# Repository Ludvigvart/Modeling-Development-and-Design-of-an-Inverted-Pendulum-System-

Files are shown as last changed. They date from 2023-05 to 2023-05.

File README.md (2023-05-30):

# Modeling-Development-and-Design-of-an-Inverted-Pendulum-System-
Repository for a bachelor's project by a group of students from the Norwegian University of Science and Technology

## About The Project
The inverted pendulum has made its mark as a staple in the field of control theory, making an appearance in classic mechanical systems such as the Furuta pendulum and the cart-pendulum system. This thesis focuses on the reaction wheel pendulum, more specifically the modeling, development and design of an inverted spherical pendulum actuated by two perpendicular reaction wheels. The system is developed with the overarching objective of functioning as an interactive learning platform for testing and experimenting with various control configurations.

The modeling of the system is centered around the derivation of an expression for the dynamics, which is done through the utilization of the Euler-Lagrange equations. The design process integrates a hardware and mechanical design approach, aiming to achieve optimum functionality while minimizing expenditure. Fabrication of the mechanical components entails 3D printing, and the hardware components are intricately connected onto a bespoke PCB. The implementation of the operational functionalities, e.g., Euler angle estimation and control system algorithms, is executed through the usage of the ESP32 family-based microcontroller. Additionally, wireless communication between the microcontroller and a Python-based user interface is established, making the product intuitive and user-friendly. 

<div style="display: flex; justify-content: center;">
  dual_axis_system
</div>

## Programs Used
Fusion 360 by Autodesk was used to design all 3D-printed components for the system. The microcontroller program was written in Arduino C. Altium Designer was used to design the custom PCB.
Python 3.11 was used to create the PC-program. 
* [](https://www.autodesk.no/products/fusion-360/overview)
* [](https://www.arduino.cc/en/software)
* [](https://www.altium.com/altium-designer)
* [](https://www.python.org/)

## Notes Regarding Usage
When uploading new code to microcontroller with a USB cable, it is important that the power switch on the system is in the OFF position. With the power switch ON and a USB cable connected, it is likely that the microcontroller will be damaged, as 5 V then will be supplied from two different sources. 
When charging the batteries, it is recommended that a voltage between 12.6 - 13 V is supplied with a current of approximately 2 A. We suggest that the batteries should always have a charge between 11.1 – 12.6 V to retain suitable motor performance. 

## Notes Regarding Included Files
The finalized microcontroller code can be accessed in the designated Arduino code folder. The CAD models and adjoining G-code files of the system's 3D-printed parts are made accessible within the CAD folder. The design files for the custom PCB are available under the PCB folder. A compiled executable "Inverted Pendulum Interface.exe" of the PC-program is also provided, along the full Python code. Regarding the PC-program it is worth mentioning that it’s intended to work on any Windows 10/11 PC with a screen resolution of 1920x1080 and a scaling factor set to 100%.

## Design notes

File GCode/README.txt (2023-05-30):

The G-Code files are ready to use with the settings used under the project. The last number in the file name pertains to percent infill. The 3D-print machines used are the Ultimaker 2 Extended+ series. They can also be printed on a normal Ultimaker 2+, except for the pendulums.

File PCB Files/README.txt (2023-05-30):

This folder contains the Altium Designer project files "BSc_PCB_balanserande_pinne", and a complete zip file "Gerber.rar" of all necessary Gerber files needed for production by a PCB manufacturer.

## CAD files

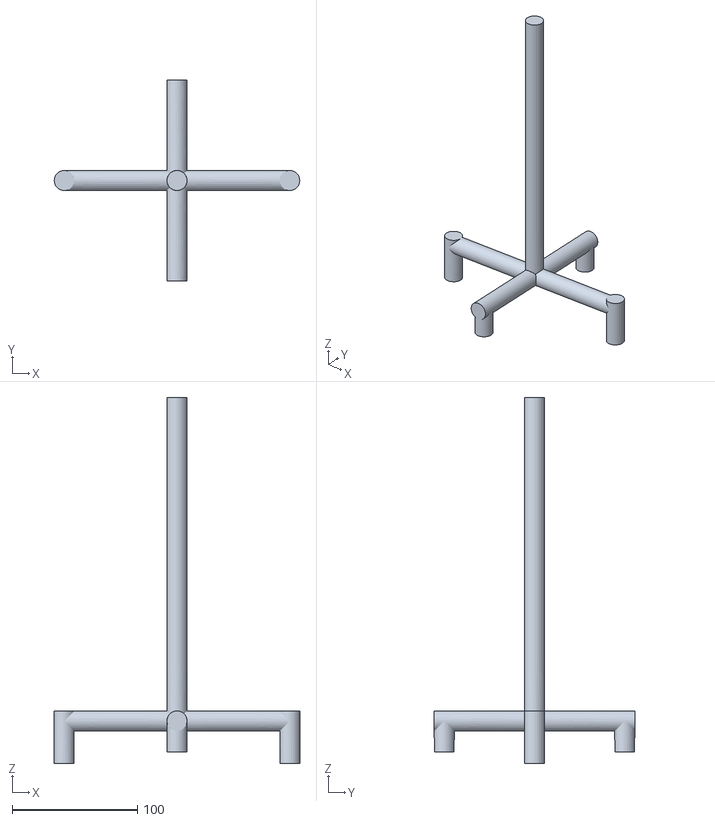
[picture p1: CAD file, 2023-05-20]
STL Files/Quad-Ended Pendulum v1.stl
196.0 x 160.0 x 292.0

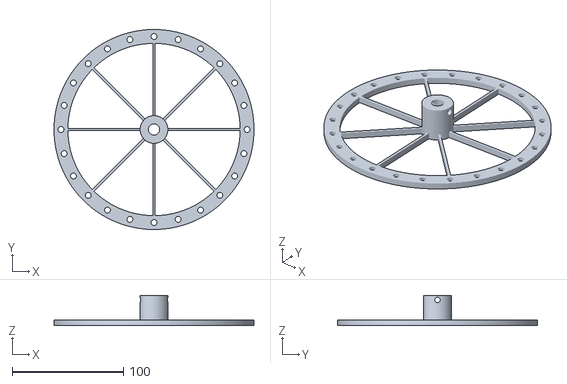
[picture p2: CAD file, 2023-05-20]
STL Files/Reaction Wheel v1.stl
180.0 x 180.0 x 27.0

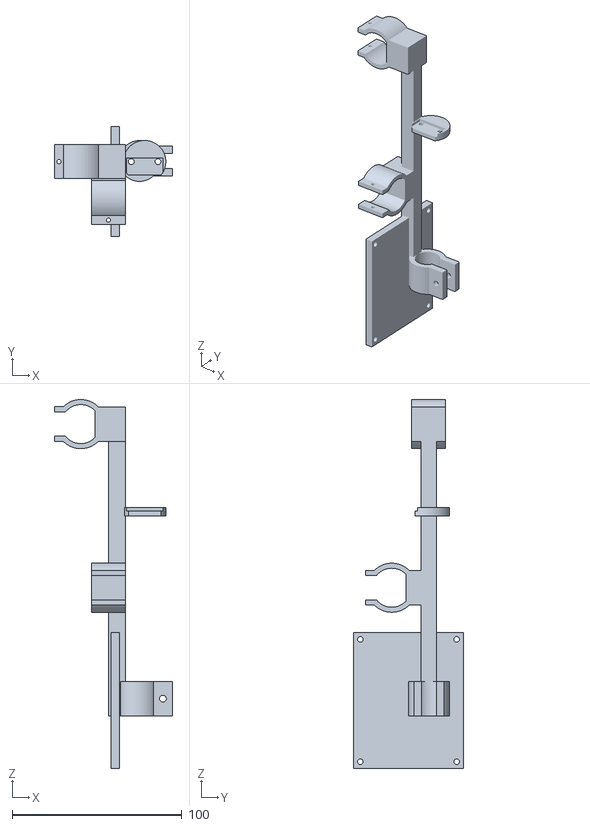
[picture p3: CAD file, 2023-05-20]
STL Files/Frame v3.stl
69.6 x 64.8 x 217.6

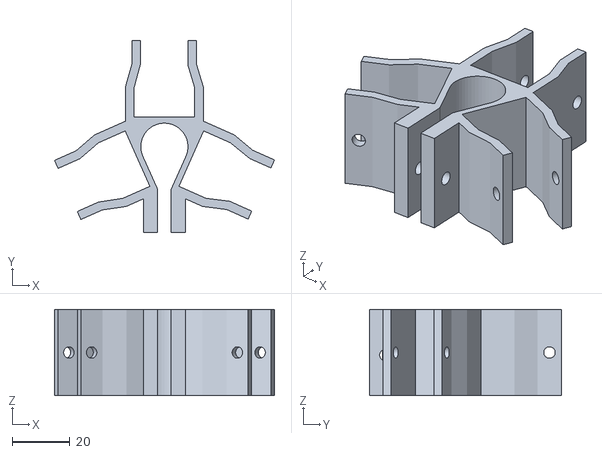
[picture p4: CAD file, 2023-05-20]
STL Files/Battery Mount v1.stl
76.5 x 66.7 x 30.0

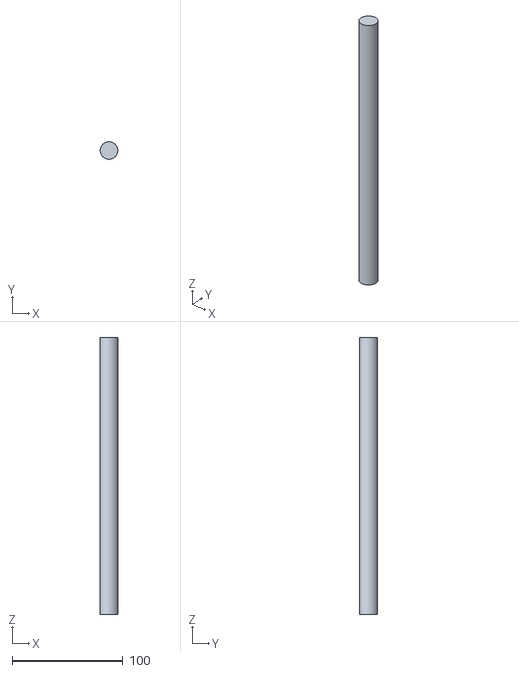
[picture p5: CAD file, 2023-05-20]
STL Files/Pendulum.stl
16.0 x 16.0 x 250.0

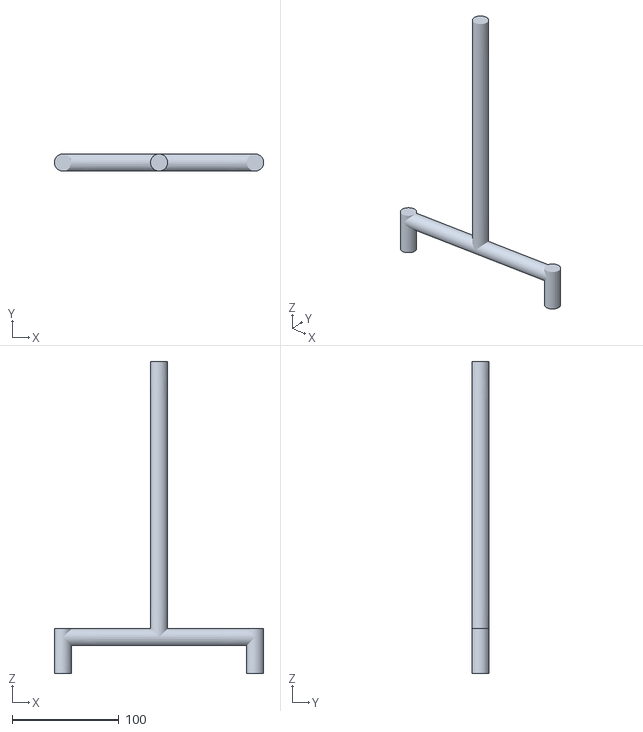
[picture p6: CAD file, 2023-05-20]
STL Files/Double-Ended Pendulum v1.stl
195.9 x 16.0 x 292.0

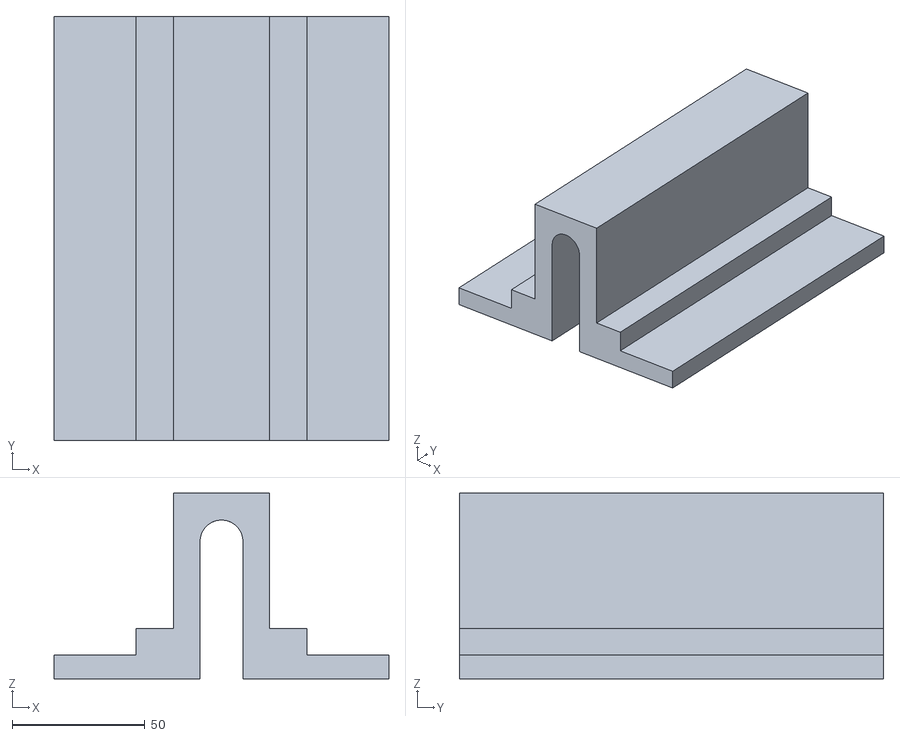
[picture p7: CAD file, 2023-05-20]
STL Files/Stabilization tool v2.stl
126.4 x 160.0 x 70.0

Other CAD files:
CAD Models/Battery Mount v1.f3d
CAD Models/Double-Ended Pendulum v1.f3d
CAD Models/Frame v3.f3z
CAD Models/IMU - Platform v1.f3d
CAD Models/Main Hold v1.f3d
CAD Models/Motor Mount v1.f3d
CAD Models/PCB Mount v1.f3d
CAD Models/Quad-Ended Pendulum v1.f3d
CAD Models/Reaction Wheel v1.f3d
CAD Models/Stabilization tool v2.f3d
STL Files/Pendulum.f3d

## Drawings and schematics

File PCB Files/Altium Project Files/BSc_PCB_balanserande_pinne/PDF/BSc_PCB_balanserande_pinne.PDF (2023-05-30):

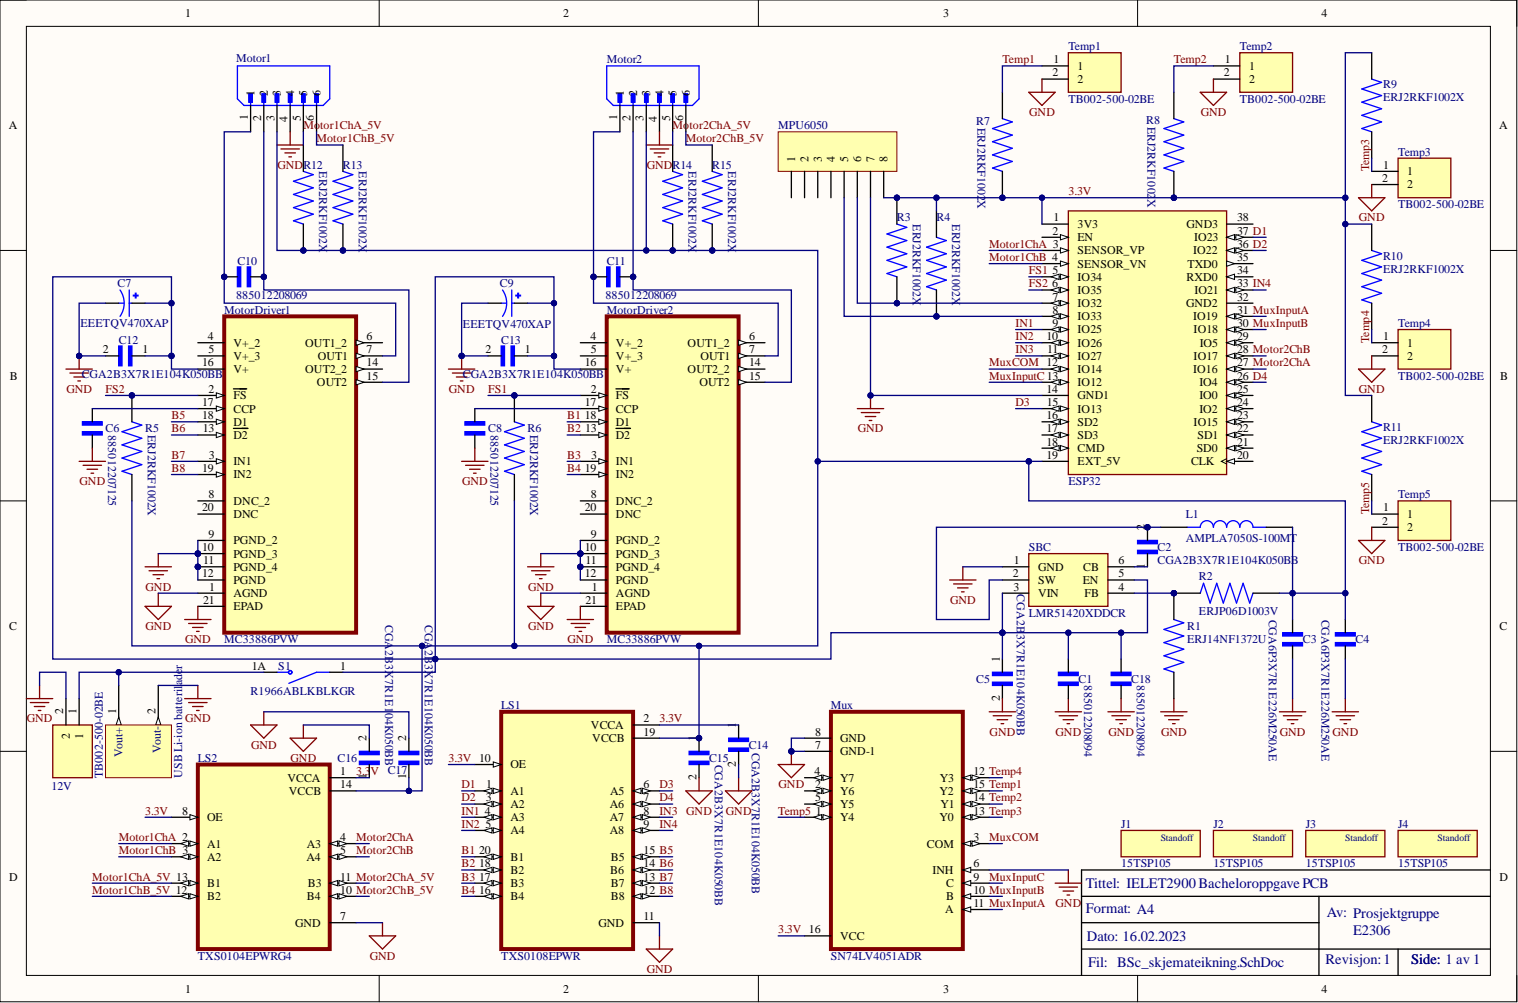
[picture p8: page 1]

USB Li-ion batterilader

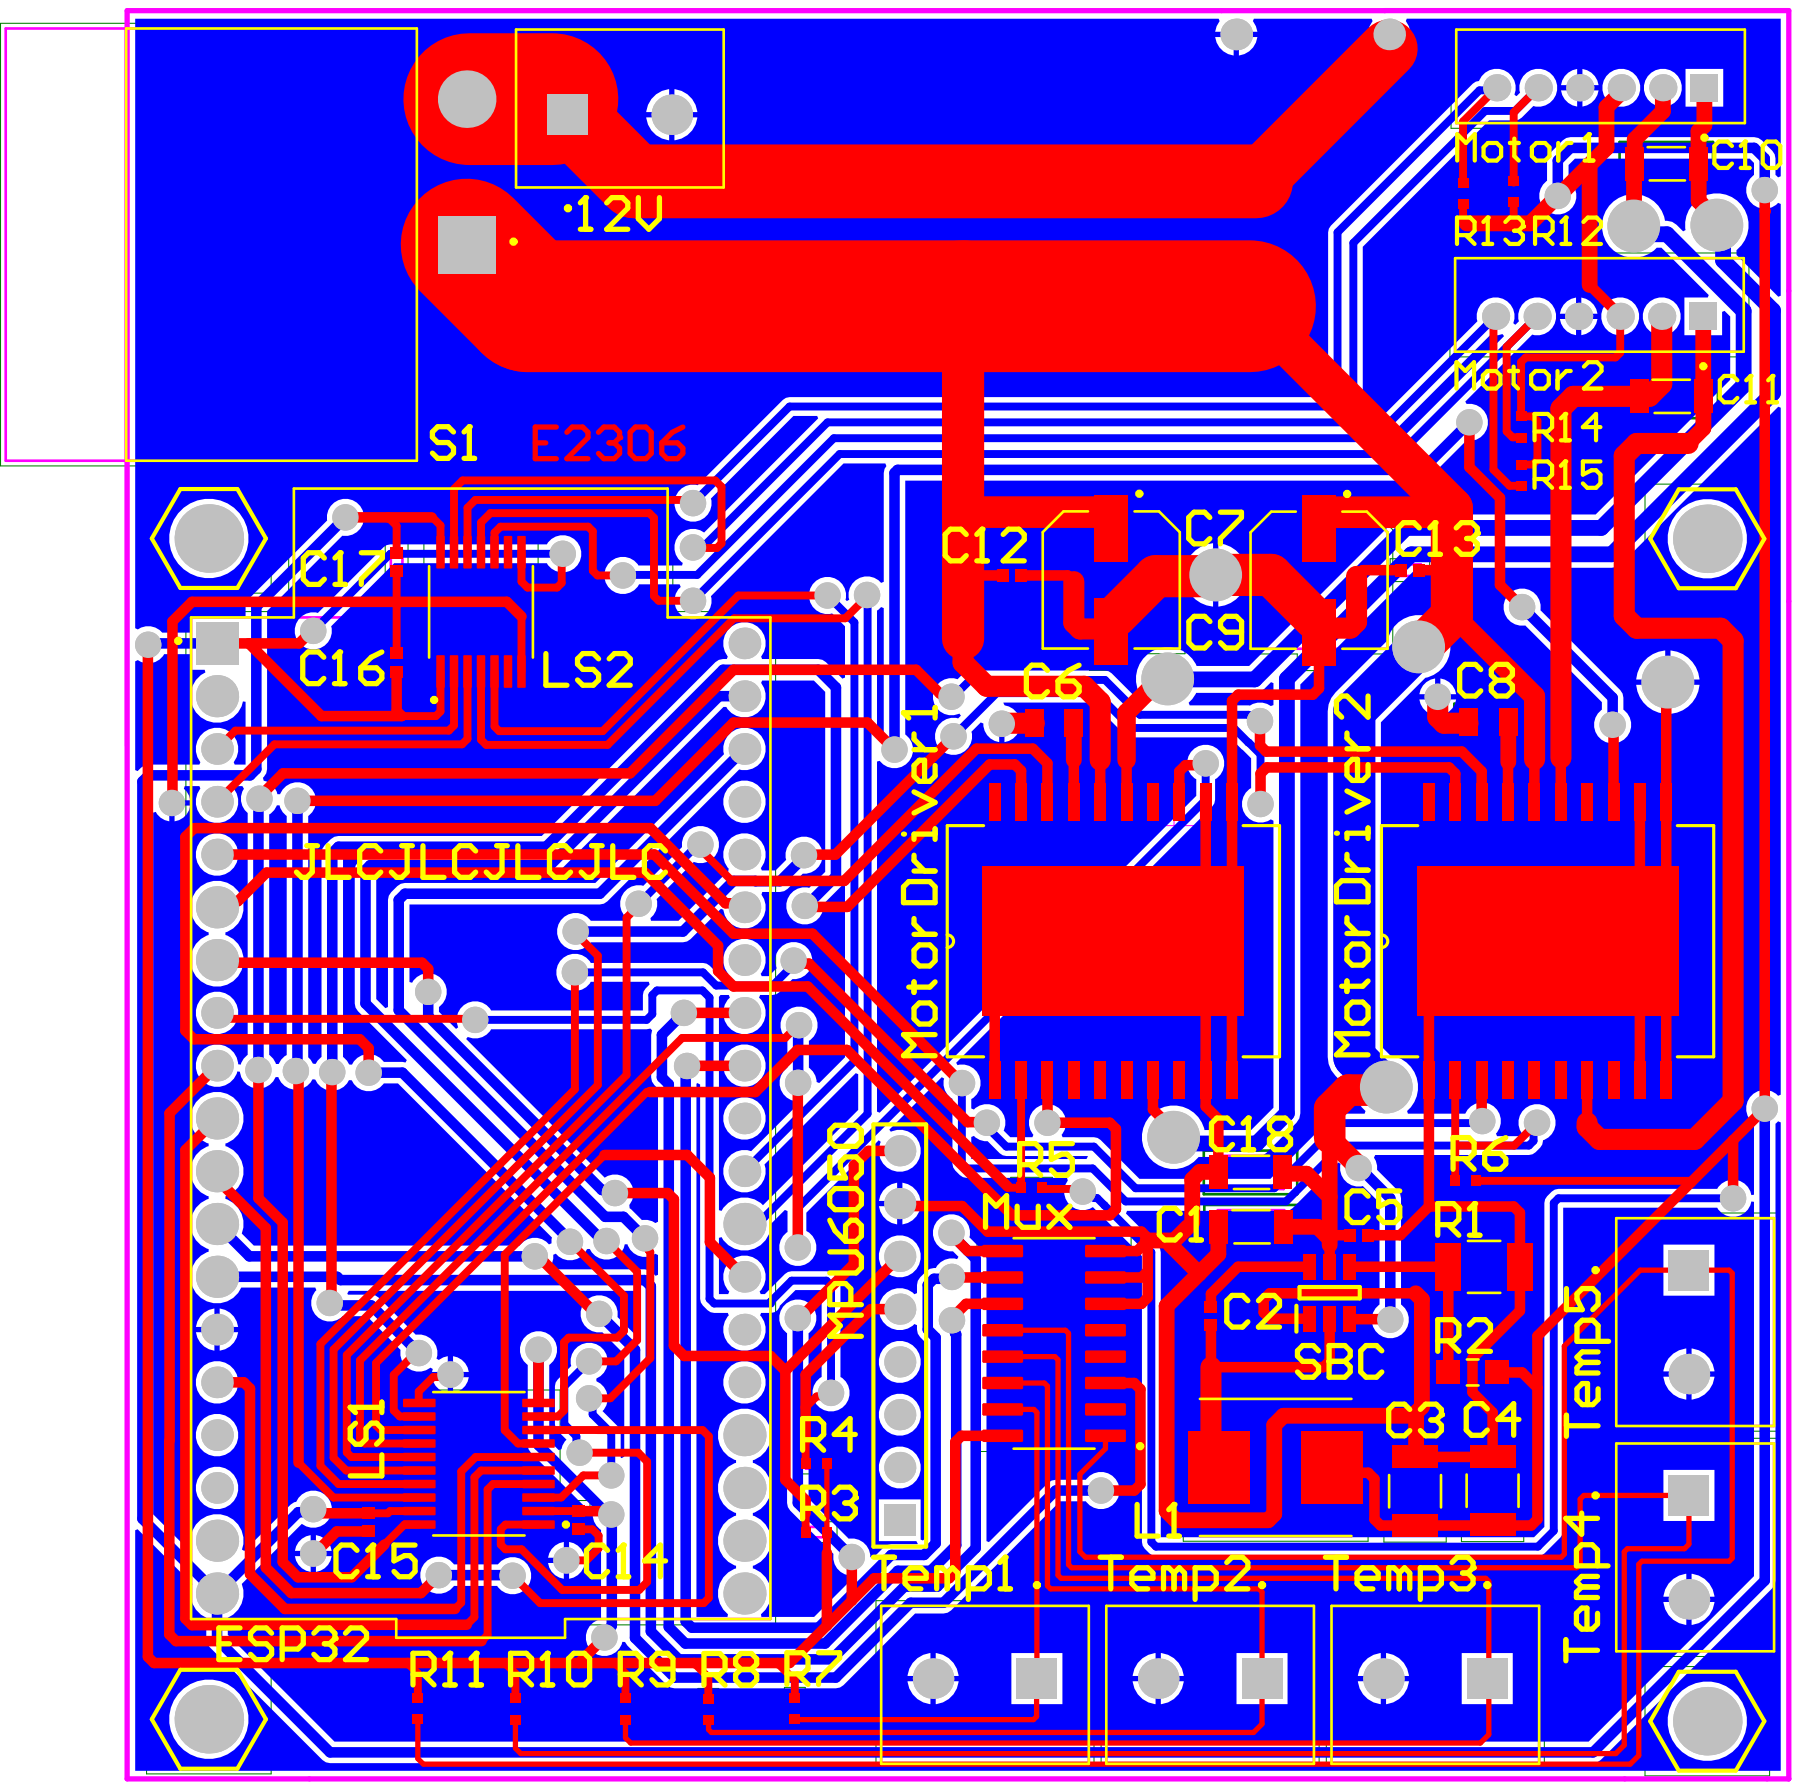
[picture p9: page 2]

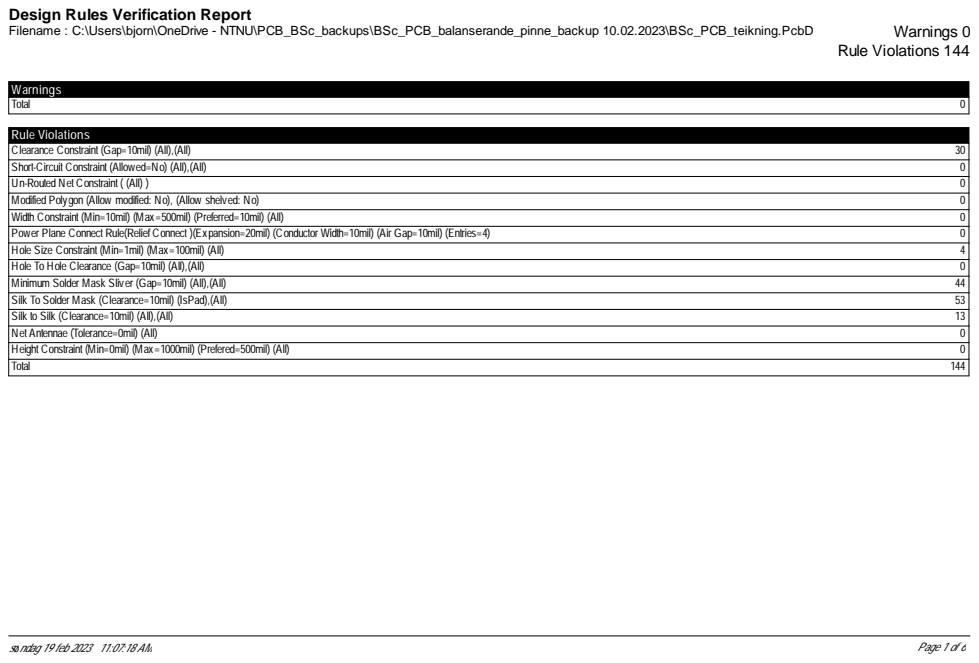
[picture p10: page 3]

Design Rules Verification Report

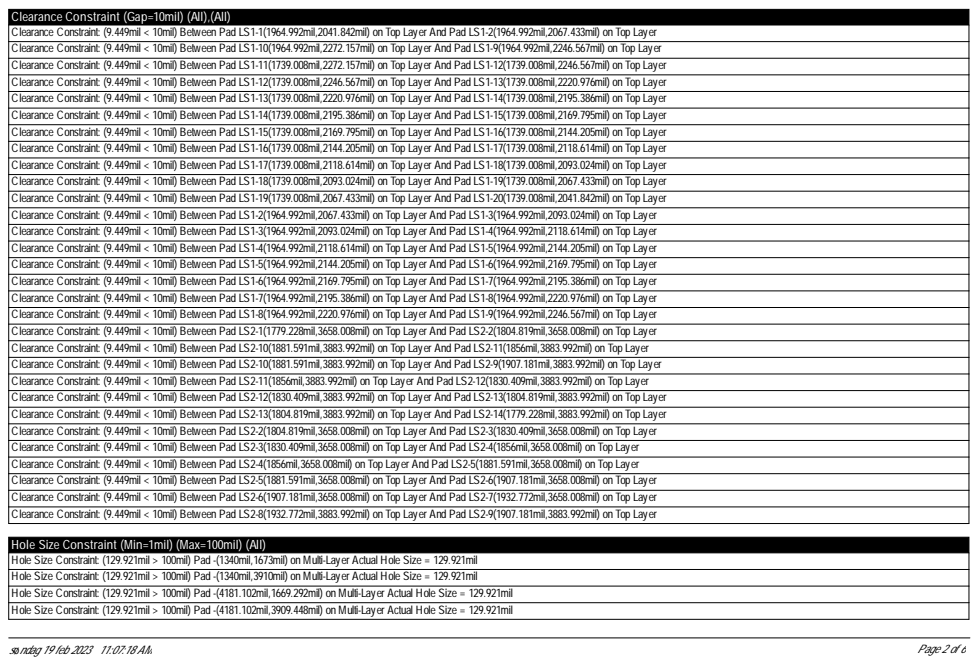
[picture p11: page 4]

Clearance Constraint (Gap=10mil) (All),(All)
Clearance Constraint: (9.449mil < 10mil) Between Pad LS1-1(1964.992mil,2041.842mil) on Top Layer And Pad LS1-2(1964.992mil,2067.433mil) on Top Layer
Clearance Constraint: (9.449mil < 10mil) Between Pad LS1-10(1964.992mil,2272.157mil) on Top Layer And Pad LS1-9(1964.992mil,2246.567mil) on Top Layer
Clearance Constraint: (9.449mil < 10mil) Between Pad LS1-11(1739.008mil,2272.157mil) on Top Layer And Pad LS1-12(1739.008mil,2246.567mil) on Top Layer
Clearance Constraint: (9.449mil < 10mil) Between Pad LS1-12(1739.008mil,2246.567mil) on Top Layer And Pad LS1-13(1739.008mil,2220.976mil) on Top Layer
Clearance Constraint: (9.449mil < 10mil) Between Pad LS1-13(1739.008mil,2220.976mil) on Top Layer And Pad LS1-14(1739.008mil,2195.386mil) on Top Layer
Clearance Constraint: (9.449mil < 10mil) Between Pad LS1-14(1739.008mil,2195.386mil) on Top Layer And Pad LS1-15(1739.008mil,2169.795mil) on Top Layer
Clearance Constraint: (9.449mil < 10mil) Between Pad LS1-15(1739.008mil,2169.795mil) on Top Layer And Pad LS1-16(1739.008mil,2144.205mil) on Top Layer
Clearance Constraint: (9.449mil < 10mil) Between Pad LS1-16(1739.008mil,2144.205mil) on Top Layer And Pad LS1-17(1739.008mil,2118.614mil) on Top Layer
Clearance Constraint: (9.449mil < 10mil) Between Pad LS1-17(1739.008mil,2118.614mil) on Top Layer And Pad LS1-18(1739.008mil,2093.024mil) on Top Layer
Clearance Constraint: (9.449mil < 10mil) Between Pad LS1-18(1739.008mil,2093.024mil) on Top Layer And Pad LS1-19(1739.008mil,2067.433mil) on Top Layer
Clearance Constraint: (9.449mil < 10mil) Between Pad LS1-19(1739.008mil,2067.433mil) on Top Layer And Pad LS1-20(1739.008mil,2041.842mil) on Top Layer
Clearance Constraint: (9.449mil < 10mil) Between Pad LS1-2(1964.992mil,2067.433mil) on Top Layer And Pad LS1-3(1964.992mil,2093.024mil) on Top Layer
Clearance Constraint: (9.449mil < 10mil) Between Pad LS1-3(1964.992mil,2093.024mil) on Top Layer And Pad LS1-4(1964.992mil,2118.614mil) on Top Layer
Clearance Constraint: (9.449mil < 10mil) Between Pad LS1-4(1964.992mil,2118.614mil) on Top Layer And Pad LS1-5(1964.992mil,2144.205mil) on Top Layer
Clearance Constraint: (9.449mil < 10mil) Between Pad LS1-5(1964.992mil,2144.205mil) on Top Layer And Pad LS1-6(1964.992mil,2169.795mil) on Top Layer
Clearance Constraint: (9.449mil < 10mil) Between Pad LS1-6(1964.992mil,2169.795mil) on Top Layer And Pad LS1-7(1964.992mil,2195.386mil) on Top Layer
Clearance Constraint: (9.449mil < 10mil) Between Pad LS1-7(1964.992mil,2195.386mil) on Top Layer And Pad LS1-8(1964.992mil,2220.976mil) on Top Layer
Clearance Constraint: (9.449mil < 10mil) Between Pad LS1-8(1964.992mil,2220.976mil) on Top Layer And Pad LS1-9(1964.992mil,2246.567mil) on Top Layer
Clearance Constraint: (9.449mil < 10mil) Between Pad LS2-1(1779.228mil,3658.008mil) on Top Layer And Pad LS2-2(1804.819mil,3658.008mil) on Top Layer
Clearance Constraint: (9.449mil < 10mil) Between Pad LS2-10(1881.591mil,3883.992mil) on Top Layer And Pad LS2-11(1856mil,3883.992mil) on Top Layer
Clearance Constraint: (9.449mil < 10mil) Between Pad LS2-10(1881.591mil,3883.992mil) on Top Layer And Pad LS2-9(1907.181mil,3883.992mil) on Top Layer
Clearance Constraint: (9.449mil < 10mil) Between Pad LS2-11(1856mil,3883.992mil) on Top Layer And Pad LS2-12(1830.409mil,3883.992mil) on Top Layer
Clearance Constraint: (9.449mil < 10mil) Between Pad LS2-12(1830.409mil,3883.992mil) on Top Layer And Pad LS2-13(1804.819mil,3883.992mil) on Top Layer
Clearance Constraint: (9.449mil < 10mil) Between Pad LS2-13(1804.819mil,3883.992mil) on Top Layer And Pad LS2-14(1779.228mil,3883.992mil) on Top Layer
Clearance Constraint: (9.449mil < 10mil) Between Pad LS2-2(1804.819mil,3658.008mil) on Top Layer And Pad LS2-3(1830.409mil,3658.008mil) on Top Layer
Clearance Constraint: (9.449mil < 10mil) Between Pad LS2-3(1830.409mil,3658.008mil) on Top Layer And Pad LS2-4(1856mil,3658.008mil) on Top Layer
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

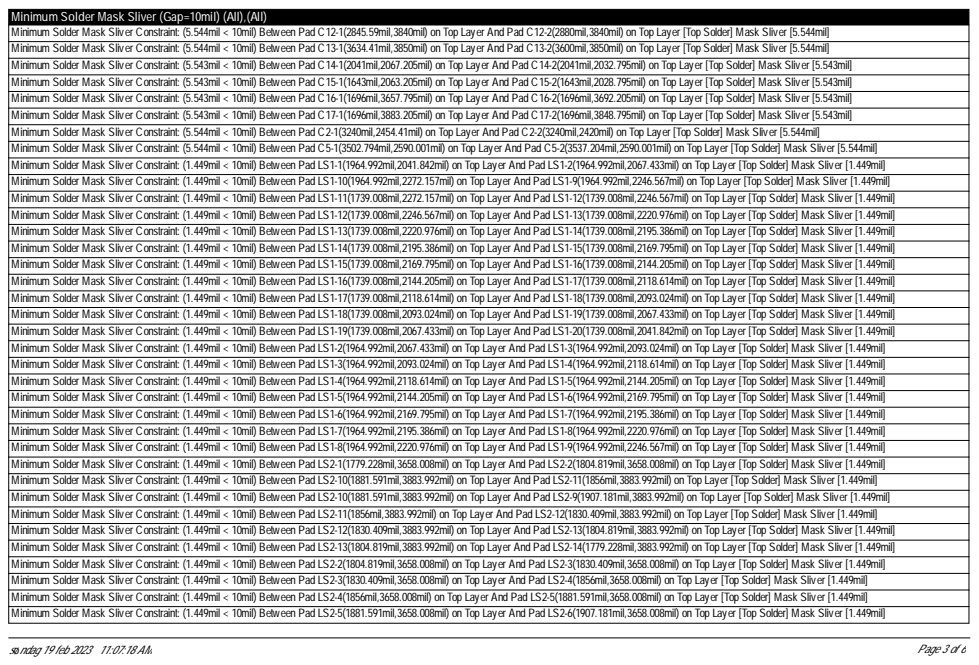
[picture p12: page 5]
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

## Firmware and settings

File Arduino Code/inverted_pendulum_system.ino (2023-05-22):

/* ========= Copyright (C) CCBY 2023 by Ivo Tredal, Leidulv Tønnesland, Ludvig Vartdal & Bjørn K.T. Solheim ==========*/

/*==================================================== Libraries =====================================================*/
#include <Wire.h>
#include <Adafruit_MPU6050.h>
#include <Adafruit_Sensor.h>
#include "BluetoothSerial.h"
/*========================================== Global Variables & Definitions ==========================================*/

// Pinouts
#define i2cSda 33
#define i2cScl 32
#define in1 25
#define in2 26
#define in3 27
#define in4 21
#define d1 23
#define d2 22
#define d3 13
#define d4 4
#define fs1 34
#define fs2 35
#define muxA 19
#define muxB 18
#define muxC 12
#define muxCOM 14
#define motor1EncoderChannelA 36
#define motor1EncoderChannelB 39
#define motor2EncoderChannelA 16
#define motor2EncoderChannelB 17

// General code definitions
#define oneMinute 60               // milliseconds
#define absoluteZero -273.15       // degrees celcius 
#define gravityAccel 9.81          // meters pr. second squared
const uint16_t OneRotation = 360;  // degrees  
const uint8_t noRotation = 0;                     
const uint8_t cwRotation = 1;                       
const int8_t ccwRotation = -1;
                    
// Temperature sensor properties
const float R10k = 10000.0; 
const float beta25 = 3977.0; 
const float temp25 = 298.15; 
const float R25 = 10000.0; 
const float analogmax = 4095.0; 
const float Voltage = 3.3; 
const float A = 0.001152861;
const float B = 0.000227214;
const float C = 0.000000610;
const float D = 0.000000072;
const uint8_t numberOfTempSensor = 5;
float temp[5];
float tempCelsius;

// Enocder variables
volatile uint8_t currStateMotor1EncoderA;
volatile uint8_t currStateMotor2EncoderA;
volatile uint8_t prevStateMotor1EncoderA;
volatile uint8_t prevStateMotor2EncoderA;

// Timers & Intervals
unsigned long prevRPMTimer = 0;
unsigned long prevIMUTimer = 0;
unsigned long process0StartTime = 0;
unsigned long prevBluetoothTimer = 0;
unsigned long prevParamterizeMotorTimer = 0;
unsigned long prevTemperatureTimer = 0;
unsigned long prevRegulator1SampleTime = 0;
unsigned long prevRegulator2SampleTime = 0;
const unsigned long imuSampleTime = 10000;                 // microseconds
const unsigned long regulationSampleTime = 10000;          // microseconds
const unsigned long rpmSampleTime = 100000;                // microseconds
const unsigned long bluetoothUpdateInterval = 10000;       // microseconds
const unsigned long temperatureUpdateInterval = 1000000;   // microseconds
const unsigned long parameterizeMotorSampleTime = 2000000; // microseconds

// Motor settings & definitions
#define freqPWM 1000
#define motor1Channel 0
#define motor2Channel 1
#define resolutionPWM 8
const uint8_t minDutyCycle = 0;
const uint8_t maxDutyCycle = 255;
const uint8_t dutyCycleOffset = 30;
const uint8_t angleIncrement = 3;  // approximation in degrees
  
// Motor structure & properties
typedef union motor_t {
    struct motorProperties{
        double rpm;
        double angle;
        double rotation;
        double runningAngle;
        double temperature;
        double driverTemperature;
    }data;
    double motor_a[6];
};

// IMU structure & properties
struct gyroProperties{
    float x;
    float y;
    float z;
    float roll;
    float pitch;
    float xError;
    float yError;
    float zError;
    float dRoll;
    float dPitch;
    float calibrSumX;
    float calibrSumY;
    float calibrSumZ;
};

struct accelProperties{
    float x;
    float y;
    float z;
    float roll;
    float pitch;
    float xError;
    float yError;
    float zError;
    float xFiltered;
    float yFiltered;
    float zFiltered;
    float xPrev;
    float yPrev;
    float zPrev;
    float calibrSumX;
    float calibrSumY;
    float calibrSumZ;
};

typedef union imu_t {
    struct imu_s{
        gyroProperties gyro;
        accelProperties accel;
        float roll;
        float pitch;
        float rollComp;
        float pitchComp;    
        float rollPrev;
        float pitchPrev;
        float nu;
        float alpha;
    }data;
    float imu_a[34];
};

typedef union batteries_t {
    struct batteries_s {
        float battery1temp;
        float battery2temp;
        float battery3temp;
    }data;
    float batteries_a[3];
};

typedef union controller1_t {
    struct controller1_s{
        //Parameters
        float Kp;  
        float Ti;  
        float Td;
        float Tt;
        float N;
        
        //Signals
        float uP;
        float uI[2]; // uI[n], uI[n-1]
        float uD[2]; // uD[n], uD[n-1]
        float y[2];  // y[n], y[n-1]
        float u;
        float v;
        float uSat;  
    }value;
    float array[12];
};

typedef union controller2_t {
    struct controller2_s{
        //Parameters
        float Kp;  
        float Ti;  
        float Td;
        float Tt;
        float N;

        //Signals
        float uP;
        float uI[2]; // uI[n], uI[n-1]
        float uD[2]; // uD[n], uD[n-1]
        float y[2];  // y[n], y[n-1]
        float u;
        float v;
        float uSat;
    }value;
    float array[12];
};

// Transmission properties
float receiveDataArray[11];
uint8_t receiveDataCounter = 0;
const uint8_t decimalAccuracy = 3;
const uint8_t imuDataElements = 6;
const uint8_t motorDataElements = 3;
const uint8_t sendDataElements = 15;
const uint8_t motor1DataElementOffset = 6;
const uint8_t motor2DataElementOffset = 9;
const uint8_t receiveDataElements = 13;
const uint8_t receiveDataControllerElements = 3;
const uint8_t receiveDataOffset = 3;
const uint8_t batterElementOffset = 12;
const uint8_t batteryDataElements = 3;
const uint8_t PIDelementsToReceive[3] = {0,1,2};                       // PID elements to receive
const uint8_t imuElementsToSend[imuDataElements] = {3,4,16,17,30,31};  // IMU data elements to send
const uint8_t motorElementsToSend[motorDataElements] = {0,4,5};        // Motor data elements to send

// Objects
BluetoothSerial SerialBT;
TwoWire i2cImuSensor = TwoWire(0);
Adafruit_MPU6050 imuSensor;
controller1_t c1;
controller2_t c2;
imu_t imu;
batteries_t bat;
volatile motor_t motor1;
volatile motor_t motor2;

// Flags
bool runFlag = false;
bool runController1Flag = false;
bool runController2Flag = false;

// Misc. global variables for testing
uint16_t paramterizeDuctyCyle = 0;

/*====================================================== Setup =======================================================*/

void setup () {
    // Pinout configurations
    pinMode(in1, OUTPUT);
    pinMode(in2, OUTPUT);
    pinMode(d1, OUTPUT);
    pinMode(d2, OUTPUT);
    pinMode(in3, OUTPUT);
    pinMode(in4, OUTPUT);
    pinMode(d3, OUTPUT);
    pinMode(d4, OUTPUT);
    pinMode(fs1, INPUT);
    pinMode(fs2, INPUT);
    pinMode(motor1EncoderChannelA, INPUT);
    pinMode(motor1EncoderChannelB, INPUT);
    pinMode(motor2EncoderChannelA, INPUT);
    pinMode(motor2EncoderChannelB, INPUT);
    pinMode(muxA, OUTPUT);
    pinMode(muxB, OUTPUT);
    pinMode(muxC, OUTPUT);
    pinMode(muxCOM, INPUT);
    attachInterrupt(motor1EncoderChannelA, isrMotor1Encoder, CHANGE);  
    attachInterrupt(motor2EncoderChannelA, isrMotor2Encoder, CHANGE); 
    ledcSetup(motor1Channel, freqPWM, resolutionPWM);
    ledcSetup(motor2Channel, freqPWM, resolutionPWM);
    
    // Motor pins default configuration
    digitalWrite(d1, LOW);
    digitalWrite(d2, HIGH);
    digitalWrite(d3, LOW);
    digitalWrite(d4, HIGH);

    // Multiplexer pins default configuration
    digitalWrite(muxA, LOW);
    digitalWrite(muxB, LOW);
    digitalWrite(muxC, LOW);
    
    // Serial initializes
    SerialBT.begin("ESP32-E2306");
    Serial.begin(115200);
    
    // IMU initialize & setting ranges 
    i2cImuSensor.begin(i2cSda, i2cScl);
    imuSensor.begin(0x68, &i2cImuSensor);
    imuSensor.setAccelerometerRange(MPU6050_RANGE_2_G);
    imuSensor.setGyroRange(MPU6050_RANGE_250_DEG);
    imuSensor.setFilterBandwidth(MPU6050_BAND_21_HZ);

    // Update inital encoder states
    prevStateMotor1EncoderA = digitalRead(motor1EncoderChannelA);
    prevStateMotor2EncoderA = digitalRead(motor2EncoderChannelA);

    // Set defualt initialize values:
    imu.data.alpha = 0.05;
    imu.data.nu = 0.3;
}

/*==================================================== Functions =====================================================*/

void motorControl(uint8_t motor, float regulatorOutput) {
    int8_t direction;
    uint16_t dutyCycle;
    
    // Rounds an maps output from regulator
    int16_t regulatorOutputRounded = round((float)regulatorOutput);
    int16_t dutyCycleWithDirection = map(regulatorOutputRounded, -maxDutyCycle,maxDutyCycle, 
                                        -(maxDutyCycle-dutyCycleOffset), maxDutyCycle-dutyCycleOffset);

    // Identifies direction and sets duty cycle as positive
    if (dutyCycleWithDirection > 0) {
        direction = ccwRotation;
        dutyCycle = dutyCycleWithDirection + dutyCycleOffset;
    }
    if (dutyCycleWithDirection < 0) {
        direction = cwRotation; 
        dutyCycle = abs(dutyCycleWithDirection) + dutyCycleOffset;
    }

    // Upper and lower limit for duty cycle
    if (dutyCycleWithDirection == 0) {dutyCycle = minDutyCycle;}
    if (dutyCycle > maxDutyCycle || dutyCycle < -maxDutyCycle ) {dutyCycle = maxDutyCycle;}

    switch(motor) {
        case 1:
            if (direction == ccwRotation) {
                motor1.data.rotation = ccwRotation;
                ledcDetachPin(in3);
                digitalWrite(in3, LOW);
                ledcAttachPin(in4, motor1Channel);
                ledcWrite(motor1Channel, dutyCycle);    
            }
            if (direction == cwRotation) {
                motor1.data.rotation = cwRotation;
                ledcDetachPin(in4);
                digitalWrite(in4, LOW);
                ledcAttachPin(in3, motor1Channel);
                ledcWrite(motor1Channel, dutyCycle);            
            }
            break;
        case 2:
            if (direction == ccwRotation) {  
                motor2.data.rotation = ccwRotation;
                ledcDetachPin(in2);
                digitalWrite(in2, LOW);
                ledcAttachPin(in1, motor2Channel);
                ledcWrite(motor2Channel, dutyCycle);
            }
            if (direction == cwRotation) {
                motor2.data.rotation = cwRotation;
                ledcDetachPin(in1);
                digitalWrite(in1, LOW);
                ledcAttachPin(in2, motor2Channel);
                ledcWrite(motor2Channel, dutyCycle);  
            }
            break;
    }
}


void imuGetData(){
    unsigned long currentIMUTimer = esp_timer_get_time();

    if(currentIMUTimer-prevIMUTimer >= imuSampleTime) {
        sensors_event_t a, g, temp;
        imuSensor.getEvent(&a, &g, &temp);
          
        // Get raw data and correct for error
        imu.data.accel.x = a.acceleration.x - imu.data.accel.xError;
        imu.data.accel.y = a.acceleration.y - imu.data.accel.yError;
        imu.data.accel.z = a.acceleration.z - imu.data.accel.zError;
        imu.data.gyro.x = g.gyro.x - imu.data.gyro.xError;
        imu.data.gyro.y = g.gyro.y - imu.data.gyro.yError;
        imu.data.gyro.z = g.gyro.z - imu.data.gyro.zError;

        // Filter accelerometer data (EWMA)
        imu.data.accel.xFiltered = imu.data.nu * imu.data.accel.x + (1 - imu.data.nu) * imu.data.accel.xPrev;
        imu.data.accel.yFiltered = imu.data.nu * imu.data.accel.y + (1 - imu.data.nu) * imu.data.accel.yPrev;
        imu.data.accel.zFiltered = imu.data.nu * imu.data.accel.z + (1 - imu.data.nu) * imu.data.accel.zPrev;

        // Compute Euler angles from accelerometer
        imu.data.accel.roll = atan2(imu.data.accel.yFiltered , imu.data.accel.zFiltered);
        imu.data.accel.pitch = atan2(-imu.data.accel.xFiltered , sqrt(imu.data.accel.yFiltered * 
                                    imu.data.accel.yFiltered + imu.data.accel.zFiltered * imu.data.accel.zFiltered));

        // Transform body rate to Euler rate
        imu.data.gyro.dRoll = imu.data.gyro.x + tanf(imu.data.pitchComp) * (imu.data.gyro.y * sinf(imu.data.rollComp) 
                              + imu.data.gyro.z * cosf(imu.data.rollComp));
        imu.data.gyro.dPitch = imu.data.gyro.y * cosf(imu.data.rollComp) - imu.data.gyro.z * sinf(imu.data.rollComp);
    
        // Compute Euler angles from gyroscope
        imu.data.gyro.roll = imu.data.rollPrev + (imuSampleTime/1e6) * imu.data.gyro.dRoll;
        imu.data.gyro.pitch = imu.data.pitchPrev + (imuSampleTime/1e6) * imu.data.gyro.dPitch;
        
        // Applying complementary filter
        imu.data.roll = imu.data.alpha * imu.data.accel.roll + (1 - imu.data.alpha) * imu.data.gyro.roll;
        imu.data.pitch = imu.data.alpha * imu.data.accel.pitch + (1 - imu.data.alpha) * imu.data.gyro.pitch;

        // Update signals
        imu.data.accel.xPrev = imu.data.accel.xFiltered;
        imu.data.accel.yPrev = imu.data.accel.yFiltered;
        imu.data.accel.zPrev = imu.data.accel.zFiltered;
        imu.data.rollPrev = imu.data.roll;
        imu.data.pitchPrev = imu.data.pitch;
       
        prevIMUTimer = currentIMUTimer;  
    } 
}

void getMotorsRPM() {
    unsigned long currentRPMTimer = esp_timer_get_time();

    if (currentRPMTimer - prevRPMTimer >= rpmSampleTime) {
        motor1.data.rpm = ((float)abs(motor1.data.runningAngle)/(float)OneRotation)*(float)oneMinute*
                          ((float)rpmSampleTime/(float)1e4);
        motor2.data.rpm = ((float)abs(motor2.data.runningAngle)/(float)OneRotation)*(float)oneMinute*
                          ((float)rpmSampleTime/(float)1e4);
        motor1.data.runningAngle = 0;
        motor2.data.runningAngle = 0;
        
        prevRPMTimer = esp_timer_get_time();
    } 
}

// Interrupt Routine for motor 1 encoder
void isrMotor1Encoder() {
    currStateMotor1EncoderA = digitalRead(motor1EncoderChannelA); 
    if (currStateMotor1EncoderA != prevStateMotor1EncoderA) {
        if (digitalRead(motor1EncoderChannelB) != currStateMotor1EncoderA) {
            motor1.data.angle += angleIncrement;
            motor1.data.runningAngle += angleIncrement;  
            motor1.data.rotation = cwRotation;
        }
        else {
            motor1.data.angle -= angleIncrement;
            motor1.data.runningAngle -= angleIncrement;  
            motor1.data.rotation = ccwRotation;  
        }
    }
    if (motor1.data.angle >= OneRotation || motor1.data.angle <= -(OneRotation)) {
        motor1.data.angle = 0;
    }
    prevStateMotor1EncoderA = currStateMotor1EncoderA;
}

// Interrupt Routine for motor 2 encoder
void isrMotor2Encoder() {
    currStateMotor2EncoderA = digitalRead(motor2EncoderChannelA); 
    if (currStateMotor2EncoderA != prevStateMotor2EncoderA) {
        if (digitalRead(motor2EncoderChannelB) != currStateMotor2EncoderA) {
            motor2.data.angle += angleIncrement;
            motor2.data.runningAngle += angleIncrement;   
            motor2.data.rotation = cwRotation; 
        }
        else {
            motor2.data.angle -= angleIncrement;
            motor2.data.runningAngle -= angleIncrement;  
            motor2.data.rotation = ccwRotation;
        }
    }
    if (motor2.data.angle >= OneRotation || motor2.data.angle <= -(OneRotation)) {
        motor2.data.angle = 0;
    }
    prevStateMotor2EncoderA = currStateMotor2EncoderA;
}

void getTemperatures(){
    if (esp_timer_get_time() - prevTemperatureTimer >= temperatureUpdateInterval){
        for(int i = 0; i < numberOfTempSensor; i++){
            temp[i]= readMux(i);  
        }
        bat.data.battery1temp = temp[2];   
        motor1.data.driverTemperature = temp[3];
        motor2.data.driverTemperature = temp[4];
        motor1.data.temperature = temp[1];
        motor2.data.temperature = temp[0]; 
        prevTemperatureTimer = esp_timer_get_time();  
    }
}

float readMux(int channel){
    int controlPin[] = {muxA, muxB, muxC};

    int muxChannel[5][3]={
        {0,0,0}, // channel 0
        {1,0,0}, // channel 1
        {0,1,0}, // channel 2
        {1,1,0}, // channel 3
        {0,0,1}, // channel 4
    };

    // Loop through each signal
    for(int i = 0; i < 3; i ++){
        digitalWrite(controlPin[i], muxChannel[channel][i]);
    }
    // Read the value of the muxCOM pin and calculate temperature by Steinhart-Hart equation
    int raw = analogRead(muxCOM);
    float Rt = R10k / (analogmax /raw - 1.0);
    float tempCelsius = (1.0 / (A + (B * log(Rt)) + (C * pow(log(Rt), 2.0)) + (D * pow(log(Rt), 3.0)))) + absoluteZero;
    return tempCelsius;
}

// Simple manual parameterization function for motor to find correlation between duty cycle and RPM
void parameterizeMotor() {
    
    if (esp_timer_get_time() - prevParamterizeMotorTimer >= parameterizeMotorSampleTime) {
        // Motor 1 cw;
        ledcDetachPin(in4);
        digitalWrite(in4, LOW);
        ledcAttachPin(in3, motor1Channel);
        ledcWrite(motor1Channel, paramterizeDuctyCyle);      
               
        SerialBT.println("Duty cycle: " + (String)paramterizeDuctyCyle + " , RPM: " + (String)motor1.data.rpm);
        paramterizeDuctyCyle++;
        prevParamterizeMotorTimer = esp_timer_get_time();
    } 
}

void calibrateImu() {
    // Find errors values for gyroscope and accelerometer
    for (float i=1.00; i < 1000; i++) {
        sensors_event_t a, g, temp;
        imuSensor.getEvent(&a, &g, &temp);
        imu.data.gyro.calibrSumX += g.gyro.x;
        imu.data.gyro.xError = imu.data.gyro.calibrSumX/i;
        imu.data.gyro.calibrSumY += g.gyro.y;
        imu.data.gyro.yError = imu.data.gyro.calibrSumY/i;
        imu.data.gyro.calibrSumZ += g.gyro.z;
        imu.data.gyro.zError = imu.data.gyro.calibrSumZ/i;       
        imu.data.accel.calibrSumX += a.acceleration.x;
        imu.data.accel.xError = imu.data.accel.calibrSumX/i;
        imu.data.accel.calibrSumY += a.acceleration.y;
        imu.data.accel.yError = imu.data.accel.calibrSumY/i;
        imu.data.accel.calibrSumZ += a.acceleration.z - gravityAccel;
        imu.data.accel.zError = imu.data.accel.calibrSumZ/i;         
    }
    SerialBT.println(1); // Indicate that calibartion is done            
}


// Single-axis SISO PID control
void singleAxis() {
    unsigned long currentRegulationTimer = esp_timer_get_time();
    unsigned long Ts = currentRegulationTimer - prevRegulator1SampleTime;

    if(Ts >= regulationSampleTime){
        // Parameters
        c1.value.N = 10;
        c1.value.Tt = sqrt(c1.value.Td*c1.value.Ti);
        float chi = (Ts/1e6) / (c1.value.Tt);
        float sigma = (Ts/1e6) / (c1.value.Ti);
        float xi = ((Ts/1e6)*c1.value.N - 2*c1.value.Td) / ((Ts/1e6)*c1.value.N + 2*c1.value.Td);
        float zeta = (2*c1.value.Td*c1.value.N) / ((Ts/1e6)*c1.value.N + 2*c1.value.Td);

        //Fetch output data
        c1.value.y[0] = imu.data.pitch;

        //Compute inputs
        c1.value.uP = -c1.value.Kp * c1.value.y[0];
        c1.value.uI[0] = c1.value.uI[1] - c1.value.Kp * sigma * c1.value.y[0];
        c1.value.uD[0] = -xi * c1.value.uD[1] - c1.value.Kp * zeta * (c1.value.y[0] - c1.value.y[1]);
        c1.value.v = c1.value.uP + c1.value.uI[0] + c1.value.uD[0];  
        c1.value.uI[0] += chi * (constrain(c1.value.v, -maxDutyCycle, maxDutyCycle) - c1.value.v);
        c1.value.u = c1.value.uP + c1.value.uI[0] + c1.value.uD[0]; 
        c1.value.uSat = constrain(c1.value.u, -maxDutyCycle, maxDutyCycle);
        
        motorControl(1,c1.value.uSat);

        // Update signals
        c1.value.y[1] = c1.value.y[0];
        c1.value.uI[1] = c1.value.uI[0];
        c1.value.uD[1] = c1.value.uD[0];

        prevRegulator1SampleTime = currentRegulationTimer;
    }
}
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
void loop () {
    // Wait for command from PC-program 
    while (runFlag == false) {
       SerialBT.println("0"); // Indicate bluetooth presence while waiting
       receiveDataOverBluetooth();
       if (runFlag == true) {
            break;
       }
    } 
    if (runController1Flag == true && runController2Flag != true) {singleAxis();}
    if (runController1Flag == true && runController2Flag == true) {dualAxis();}
    imuGetData();
    getMotorsRPM();
    sendDataOverBluetooth();
    receiveDataOverBluetooth();
    getTemperatures(); 
}
/*====================================================================================================================*/

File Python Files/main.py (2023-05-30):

# ========== Copyright (C) CCBY 2023 by Ivo Tredal, Leidulv Tønnesland, Ludvig Vartdal & Bjørn K.T. Solheim ========== #

if __name__ == '__main__':
    # ================================================= Libraries ======================================================
    import multiprocessing as mp
    from multiprocessing import Manager, freeze_support
    from functions import *
    # =========================================== Shared Global Variables ==============================================

    # Allow multiprocessing to take control
    mp.freeze_support()

    # Create manager for multiproccessing shared global variables
    manager = mp.Manager()

    notification = manager.Value('i', 0)  # default state = 0
    ble_device_found = manager.Value('b', False)
    ble_com_port = manager.Value('s', '')
    ble_receive_duration = manager.Value('f', 0.1)  # seconds
    ble_awaiting_to_send = manager.Value('b', False)
    ble_awaiting_to_disconnect = manager.Value('b', False)
    ble_device_is_calibrated = manager.Value('b', False)
    ble_imu_data = manager.list([0.00, 0.00, 0.00, 0.00, 0.00, 0.00])
    ble_motors_data = manager.list([0, 0, 0.0, 0.0, 0.0, 0.0])
    ble_data_to_send = manager.list([0, 0, 0, 0, 0, 0, 0, 0, 0, 0, 0, 0, 0])
    ble_updated_imu_data = manager.list([0.00, 0.00, 0.00, 0.00, 0.00, 0.00])
    ble_updated_motors_data = manager.list([0, 0, 0.0, 0.0, 0.0, 0.0])
    ble_update_batteries_data = manager.list([0.0, 0.0, 0.0])
    stop_program = manager.Value('b', False)

    # Defining a lock for multiproccessing sync of shared global variables
    lock = mp.Lock()

    # ================================================= Processes ======================================================

    # Start Bluetooth data receiver process
    ble_process = mp.Process(target=receive_ble_data, args=(ble_device_found, ble_com_port,
                             ble_updated_imu_data, ble_updated_motors_data, ble_update_batteries_data,
                             ble_awaiting_to_send, ble_awaiting_to_disconnect, ble_device_is_calibrated,
                             ble_data_to_send, notification, stop_program))
    ble_process.start()

    # Start GUI process
    gui_process = mp.Process(target=gui, args=(ble_device_found, ble_com_port, lock, ble_data_to_send,
                             ble_updated_imu_data, ble_updated_motors_data, ble_update_batteries_data,
                             ble_awaiting_to_send, ble_awaiting_to_disconnect, ble_device_is_calibrated, notification,
                             stop_program))
    gui_process.start()

    # Wait for both processes to finish
    ble_process.join()
    gui_process.join()
